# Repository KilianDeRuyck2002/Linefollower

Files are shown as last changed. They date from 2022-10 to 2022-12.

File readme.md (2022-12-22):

# LineFollower

<br />

## specifications
microcontroller: ATmega328 (Arduino Nano)
<br />
motors: Gear motor 9V - 10:1
<br />
h-bridge: Adafruit TB6612
<br />
sensors: QTR-8A
<br />
batteries: Lipo 3S 11,1V
<br />
wireless communication: HC-05
<br />
distance sensor - motors: 110mm
<br />
weight: 220g
<br />
speed: 0,906 m/s
<br />

## tips
<br />
1) Zorg dat de batterij zo dicht mogelijk bij de motoren staan. Zorg dat deze een beetje voor de hartlijn van de motoren ligt zodat de line follower geen wheelie maakt maar toch het grootste gewicht ligt bij de aandrijving.
<br />
<br />
2) Door de motoren breder uit elkaar te plaatsen kan hij de bochten makkelijker nemen.
<br />
<br />
3) Zorg dat de sensoren niet te ver en niet te dicht t.o.v. de motoren liggen. Als dit zich bevindt verder van de motoren zal je makkelijker aan een grotere snelheid komen maar kan je wel in de problemen geraken in scherpe bochten.
<br />
<br />
4) Hoe kleiner de diameter van de wielen hoe sneller de line follower zal gaan.
<br />
<br />
5) In het begin is er gebruik gemaakt van een bout maar deze bracht veel weerstand met zich mee, daarom is er overgeschakeld naar een bol (deze heeft maar 1 contactpunt met het papier, dus de weerstand is hier minimaal).
<br />
<br />
6) Bij de finaal code zal er een code te vinden zijn met library en zonder. De line follower is even snel met beide codes, alleen voor het programma kleiner te maken is het handig om met de library te werken.
<br />
<br />
7) Ook is er een finaal code geupload met een boost en brake principe, deze zal steeds voor de lange rechte stukken versnellen en dan bij de eerst volgende bocht kort remmen.
<br />
<br />
8) Tip voor de motoren, kies voor de gearmotoren 1000rpm / 30:1.
<br />
<br />

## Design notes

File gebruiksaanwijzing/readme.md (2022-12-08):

# Gebruiksaanwijzing

Zie document 

### opladen / vervangen batterijen
Deze line follower werkt met Lipo batterijen.

### draadloze communicatie
#### verbinding maken
uitleg over het verbinden van de robot met laptop / smartphone

#### commando's
debug [on/off]  
start  
stop  
set cycle [µs]  
set power [0..255]  
set diff [0..1]  
set kp [0..]  
set ki [0..]  
set kd [0..]  
calibrate black  
calibrate white  

### kalibratie
uitleg kalibratie  

### settings
De robot rijdt stabiel met volgende parameters:  

### start/stop button
uitleg locatie + werking start/stop button

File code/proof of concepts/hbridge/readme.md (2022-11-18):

# H-Bridge proof of concept

Minimale hard- & software die aantoont dat 2 motoren onafhankelijk van elkaar kunnen draaien, en (traploos) regelbaar zijn in snelheid en draairichting.

Programma:
- Voorwaarts van 0 -> 255 -> 0
- Achterwaarts van 0 -> 255 -> 0
- Links van 0 -> 255 -> 0
- Rechts van 0 -> 255 -> 0

Sidenote: DRV8833 mag een maximale spanning van 10,8V bedragen.
- Indien dit hoger is, dan zal de bluetooth module maar 3 weken meegaan zoals in mijn geval geweest.

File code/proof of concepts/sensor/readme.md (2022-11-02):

# Sensoren proof of concept

minimale hard- en software die aantoont dat minimaal 6 sensoren onafhankelijk van elkaar kunnen uitgelezen worden en dat daarbij een zo groot mogelijk bereik van de AD converter benut wordt (indien van toepassing)

Programma:
- Uitlezing van (8) sensoren => (QTR-8A)

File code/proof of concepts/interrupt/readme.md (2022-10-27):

# start/stop interrupt proof of concept
Minimale hard- en software die de correcte werking van een start/stop drukknop aantoont, gebruik makend van een hardware interrupt

Programma:
- Led in het begin uit
- Indien er op de interrupt knop wordt geklikt zal de status van de led veranderen
  - Van low naar high (led gaat aan)
  - Van high naar low (led gaat uit)

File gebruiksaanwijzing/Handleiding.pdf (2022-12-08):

# Handleiding Line follower

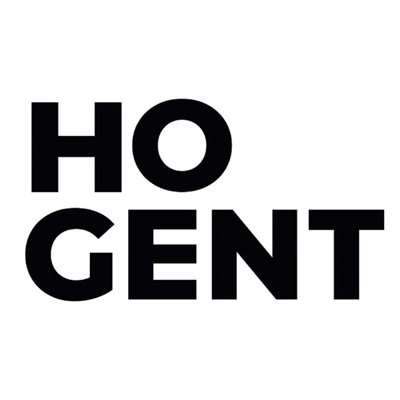
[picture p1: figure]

Naam: De Ruyck
Voornaam: Kilian
Klasgroep: 3AMB

## Gebruik van de line follower

Voor de line follower te laten rijden moeten eerst alle parameters worden ingesteld en moeten de sensoren worden gekalibreerd.

Kalibreren
Voor de sensoren te kalibreren moet er in de seriële monitor via de computer of bluetooth module het commando “calibrate white” of “calibrate black” worden getypt. Indien het commando is doorgestuurd zal deze de waarden opslaan. Zorg er wel voor dat de line follower op een volledige witte ondergrond staat om de witte waarden op te slaan en bij de zwarte waarden op een volledige zwarte ondergrond.

Rijden
Nu kunnen de parameters worden doorgestuurd aan de hand van de commando’s. Met het commando “run” zal de line follower starten met rijden. Bij het commando “stop” zal deze stoppen met rijden. Indien een commando wordt doorgestuurd die fout geschreven is of onjuist is zal er een message verschijnen dat deze niet gevonden is, dus er kan niets kapot gaan door een fout commando door te sturen.

De commando’s
- “run” => Starten met rijden (dit kan ook met de knop gedaan worden)
- “stop” => Stoppen met rijden
- “debug” => Tonen van de ingestelde parameters met de waarden
- “calibrate” => Calibreren van de sensoren
- “set cycle ‘waarde’ ” => Set cycle naar ‘waarde’ (waarde moet cijfer zijn)
- “set power ‘waarde’ ” => Set power naar ‘waarde’ (waarde moet cijfer zijn)
- “set diff ‘waarde’ ” => Set diff naar ‘waarde’ (waarde moet cijfer zijn)
- “set kp ‘waarde’ ” => Set kp naar ‘waarde’ (waarde moet cijfer zijn)
- “set ki ‘waarde’ ” => Set ki naar ‘waarde’ (waarde moet cijfer zijn)
- “set kd ‘waarde’ ” => Set kd naar ‘waarde’ (waarde moet cijfer zijn)

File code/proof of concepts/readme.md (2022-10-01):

# Proof of Concepts

Een proof of concept is een combinatie van minimale hard- en software om eenvoudig aan te tonen dat iets werkt.  
Proof of concepts kunnen enerzijds als eerste poging dienen om een bepaald onderdeel van het project werkend te krijgen. Anderzijds kunnen ze tijdens het debuggen van het finale project dienen als test om eventuele hardware problemen te elimineren bij onduidelijke problemen.
<br />  
<br />
Een proof of concept bestaat uit
* een elektronisch schema (indien van toepassing)
* minimale code om de voorop gestelde zaken te demonstreren
* minimale uitleg / aandachtspunten
<br />
De elektronische schakelingen van de proof of concepts komen bij voorkeur overeen met deze van de uiteindelijke linefollower, zodat de code zonder aanpassingen op het finale project kan draaien.

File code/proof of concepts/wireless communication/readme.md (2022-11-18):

# draadloze communicatie proof of concept
minimale hard- en software waarmee aangetoond wordt dat duplex kan gecommuniceerd worden tussen de microcontroller en een [laptop|smartphone] (schappen wat niet past), gebruik makend van [programma] (in te vullen)
<br />
### configuratie
Code HC-05: 0000 of 1234

### opmerkingen
Gebruik gemaakt van de "Serial Bluetooth Terminal" app

### gebruiksaanwijzing
/

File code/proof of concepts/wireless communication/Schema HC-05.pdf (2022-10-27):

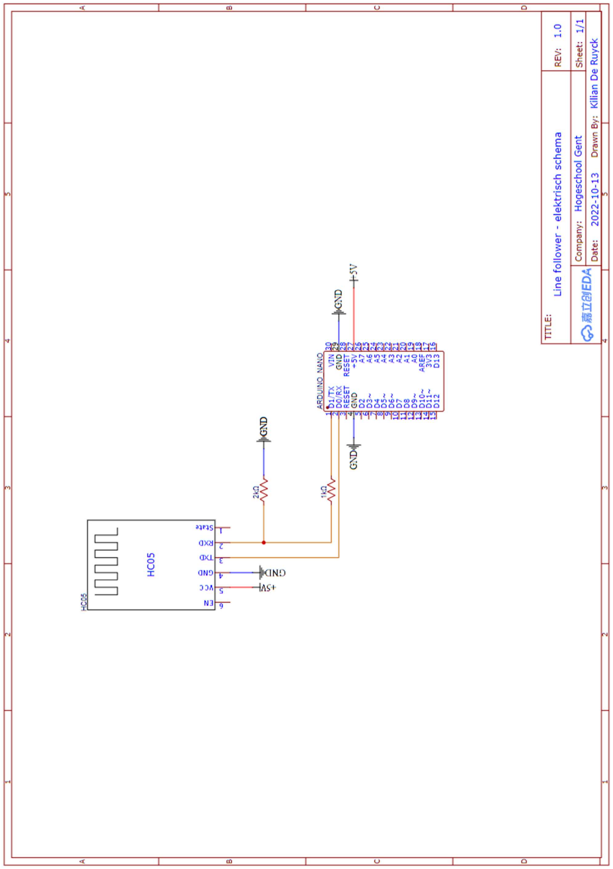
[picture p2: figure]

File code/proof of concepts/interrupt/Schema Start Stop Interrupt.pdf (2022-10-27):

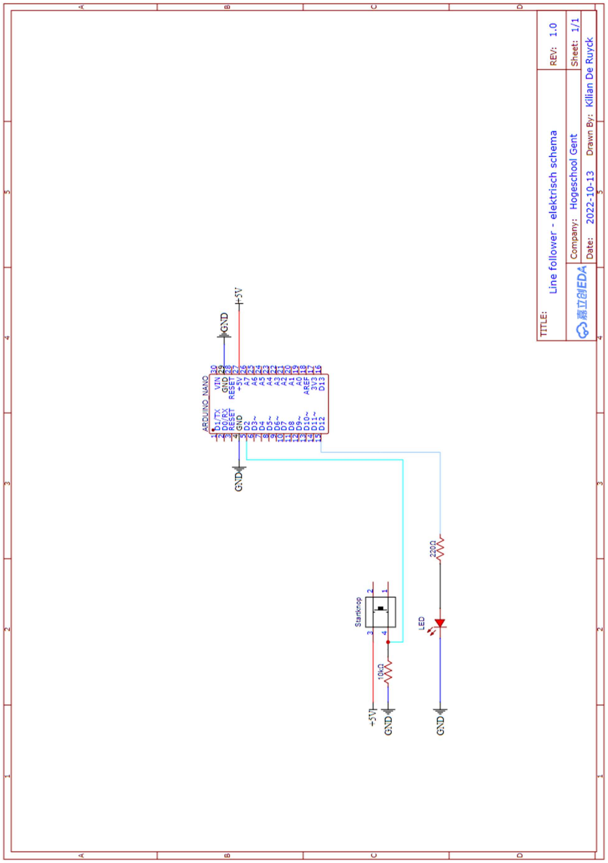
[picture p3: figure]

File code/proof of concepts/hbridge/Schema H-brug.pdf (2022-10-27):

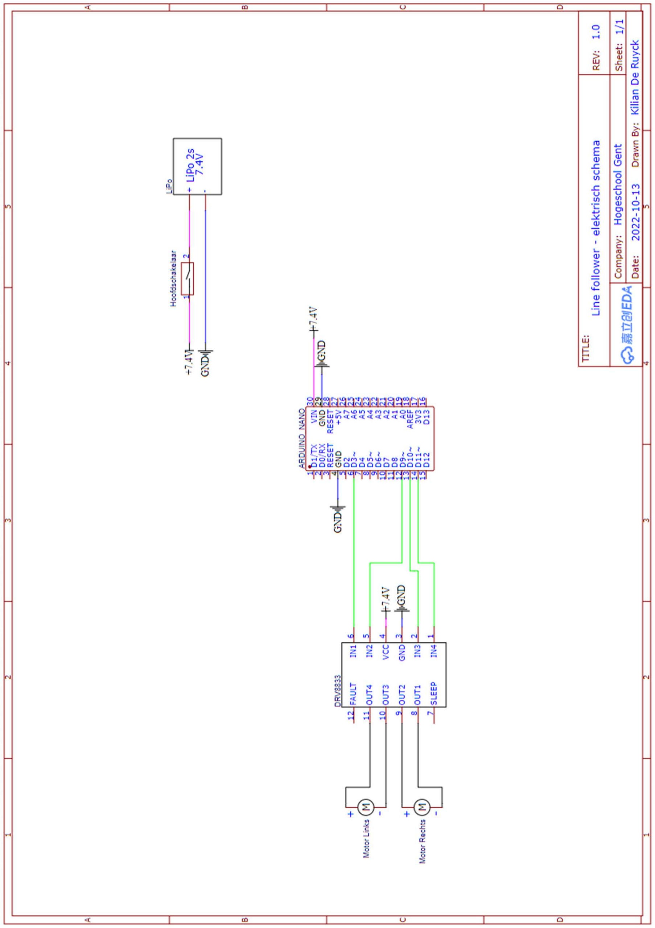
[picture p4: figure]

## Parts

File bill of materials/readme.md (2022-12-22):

## bill of materials
<br />

|Nr.  |Naam |Omschrijving |Nieuw/recup|Prijs/Stuk|Aantal|Subtotaal|
|-----|---|---|---|---|---|---|
|1 |Microcontroller	 |ATmega328 (Arduino Nano)	 |Nieuw |€ 5,4	 |1	 |€ 5,4 |
|2	  |Sensoren	 |QTR-8A	 |Nieuw |€ 11,91 |1	 |€ 11,91  |
|3	  |H-brug	 |TB6612	 |Nieuw |€ 6,5	 |1	 |€ 6,5 |
|4	  |Bluetooth module	 |HC-05	 |Nieuw |€ 4	 |1	 |€ 4 |
|5	  |Motoren	 |Gear motor 9V - 10:1	 |Nieuw |€ 5,4 |2	 |€ 10,8 |
|6	  |Wielen	 |Wielen pair 32x7mm	 |Nieuw |€ 4,32	  |1	 |€ 4,32 |
|7	  |Batterij	 |Sunpadow 3S 11,1V	 |Nieuw |€ 14,5 |1	 |€ 14,5 |
|8	  |Led	 |Led blauw 5V	 |Recup |€ 0	 |1	 |€ 0 |
|9	  |Drukknop	 |Drukknop 	 |Recup |€ 0	 |1	 |€ 0 |
|10	  |Schakelaar	 |Mini wipschakelaar AAN/UIT	 |Recup |€ 0	 |1	 |€ 0 |
|11	  |Weerstand	 |Weerstand 220Ω	 |Recup |€ 0	 |1	 |€ 0 | 
|12	  |Weerstand	 |Weerstand 1kΩ	 |Recup |€ 0	 |3	 |€ 0 |
|13	  |Weerstand	 |Weerstand 10kΩ	 |Recup |€ 0	 |1	 |€ 0 |
|14	  |Prototype Board |Double shielded board 50x70mm	 |Nieuw |€ 0,98	  |1	 |€ 0,98 |
|15	  |Frame	 |PLA	 |Nieuw |€ 0,34	  |1	 |€ 0,34 |
|16	  |Klemmenstrook	 |4 aansluitingen |Recup |€ 0 	  |1	 |€ 0 |
| | | | | |Totaal prijs:|€ 58,75  |

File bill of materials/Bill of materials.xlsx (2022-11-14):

Nr. | Naam | Omschrijving | Nieuw/Recup | Prijs/stuk | Aantal | Subtotaal | Link
1 | Microcontroller | Arduino Nano | Nieuw | 5.4 | 1 | 5.4 | https://www.amazon.nl/gp/product/B078S8BJ8T/ref=ppx_yo_dt_b_asin_title_o03_s00?ie=UTF8&psc=1
2 | Sensoren | QTR-8A | Nieuw | 11.91 | 1 | 11.91 | https://botland.store/sensors-odbiciowe/152-qtr-8a-reflectance-sensor-array-analog-pololu-960-5903351249300.html
3 | H-brug | TB6612 | Nieuw | 6.5 | 1 | 6.5 | https://www.kiwi-electronics.com/nl/adafruit-tb6612-1-2a-dc-stepper-motor-driver-breakout-board-2188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
4 | Bluetooth module | HC-05 | Nieuw | 4 | 1 | 4 | https://www.amazon.nl/gp/product/B07BHRG9KB/ref=ppx_yo_dt_b_asin_title_o03_s00?ie=UTF8&psc=1
5 | Motoren | Gear motor 9V -10:1 | Nieuw | 5.4 | 2 | 5.4 | https://botland.store/n20-micro-motors-mp-series-medium-power/12551-micro-motor-n20-bt12-10-1-1300rpm-9v-5904422306526.html
6 | Wielen | Wielen pair 32x7mm | Nieuw | 4.32 | 1 | 4.32 | https://botland.store/wheels-with-tires/12-wheels-32x7mm-black-2pcs-pololu-1087-5903351247924.html
7 | Batterij | Sunpadow 3S 11,1V | Nieuw | 14.5 | 1 | 14.5 | https://www.amazon.nl/gp/product/B08S37P8Z5/ref=ppx_yo_dt_b_asin_image_o00_s02?ie=UTF8&psc=1
8 | Led | Led blauw 5V | Recup | 0 | 1 | 0 | https://www.allekabels.be/led-diode/7369/1086017/blauwe-led-3mm-transparant-2200mcd-20ma.html
9 | Drukknop | Drukknop | Recup | 0 | 1 | 0 | https://www.otronic.nl/a-60343296/schakelaars/drukknopje-moment-6x6x4/
10 | Schakelaar | Mini wipschakelaar AAN/UIT | Recup | 0 | 1 | 0 | https://www.otronic.nl/a-62577459/schakelaars/mini-wipschakelaar-aan-uit-kcd11-250v-3a/
11 | Weerstand | Weerstand 220Ω | Recup | 0 | 1 | 0 | https://www.otronic.nl/a-59685595/weerstanden/10x-weerstand-220-ohm-1-4-watt-5-led-voorschakelweerstand/
12 | Weerstand | Weerstand 1kΩ | Recup | 0 | 3 | 0 | https://www.otronic.nl/a-59867443/weerstanden/10x-weerstand-1k-ohm-1-4-watt-5/
13 | Weerstand | Weerstand 10kΩ | Recup | 0 | 1 | 0 | https://www.otronic.nl/a-59867467/weerstanden/10x-weerstand-10k-ohm-1-4-watt-5-pull-up-pull-down/
14 | Prototype board | Double shielded board 50x70mm | Nieuw | 0.98 | 1 | 0.98 | https://botland.store/circuit-boards/2745-universal-double-sided-board-50x70mm-5904422303303.html
15 | Frame | PLA | Nieuw | 0.34 | 1 | 0.34 | /
Totaal prijs: |  |  |  |  |  | 53.35

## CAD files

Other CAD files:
technische tekeningen/mechanisch/Assembly Line follower.iam
technische tekeningen/mechanisch/Ball houder plaat.ipt
technische tekeningen/mechanisch/Bracket motoren.ipt
technische tekeningen/mechanisch/Dubbele wiel.ipt
technische tekeningen/mechanisch/Frame.ipt
technische tekeningen/mechanisch/Sensoren plaat.ipt

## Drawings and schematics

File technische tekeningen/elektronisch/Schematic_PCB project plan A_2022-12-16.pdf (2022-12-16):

# HC-05 HC⁻05 VCC

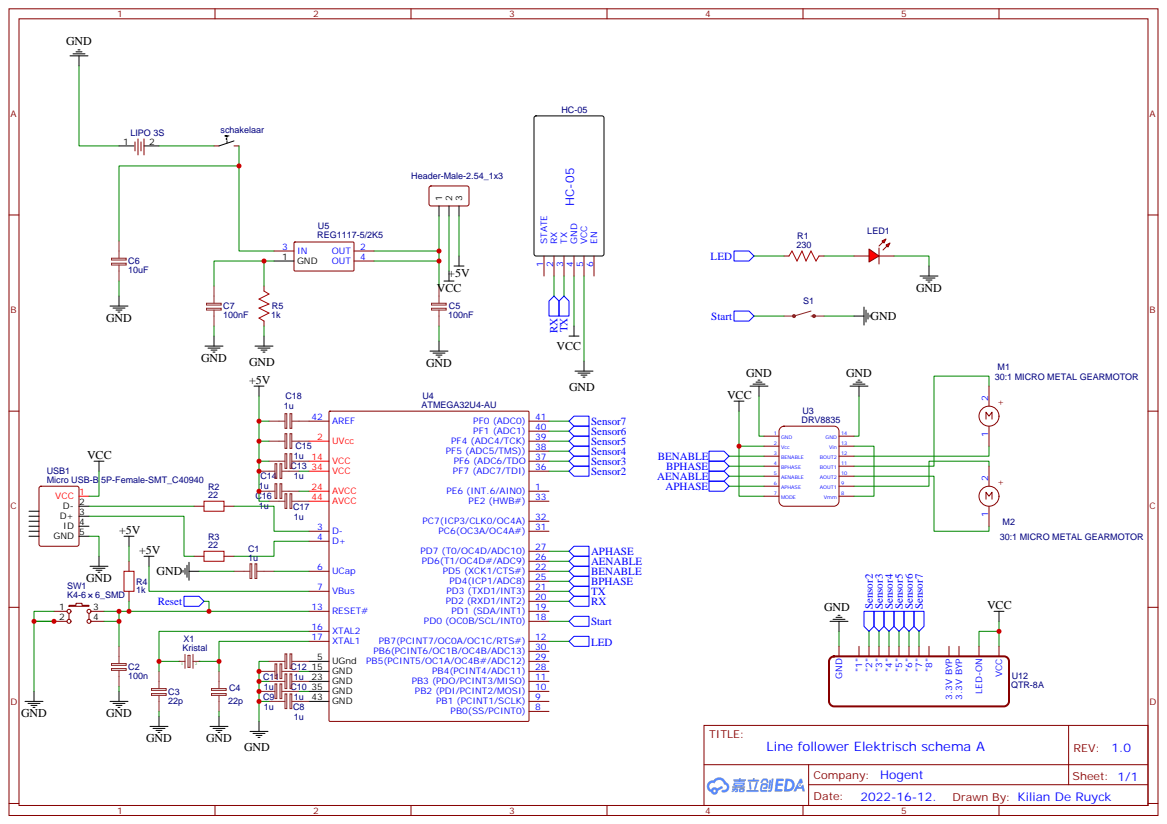
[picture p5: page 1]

PB7(PCINT7/OC0A/OC1C/RTS#) 12
PB2 (PDI/PCINT2/MOSI) 10 PB3 (PDO/PCINT3/MISO) 11 PB4(PCINT4/ADC11) 28 PB5(PCINT5/OC1A/OC4B#/ADC12) 29 PB6(PCINT6/OC1B/OC4B/ADC13) 30

Drawn By: Kilian De Ruyck

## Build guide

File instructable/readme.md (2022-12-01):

# Instructable

Een instructable is een stappenplan - zonder verdere uitleg - hoe je vertrekkend van de bill of materials en gebruik makend van de technische tekeningen de robot kan nabouwen. Ook de nodige stappen om de microcontroller te compileren en te uploaden staan beschreven.  

### stap 1
Zie document

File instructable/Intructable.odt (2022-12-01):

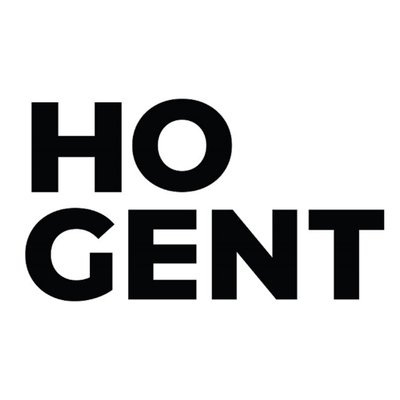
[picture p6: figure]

Intructable

Line follower

Naam: De Ruyck
Voornaam: Kilian
Klasgroep: 3AMB

Inhoudsopgave

1. Inleiding

In deze instructable wordt stap voor stap uitgelegd hoe de line follower gemaakt wordt. Hierbij zal er aan de hand van een schema uitgelegd worden hoe de verbindingen gemaakt moeten worden. Wel wordt er verwacht dat er een basiskennis is over solderen en elektriciteit.

2. Benodigdheden
- 3D-printer
- Soldeerbout
- Soldeertin
- Pinheaders male en female
- Bevestigingen (moeren, bouten en klitteband)
- USB mini kabel
- Componenten (terug te vinden in de BOM)
3. Elektrische schema

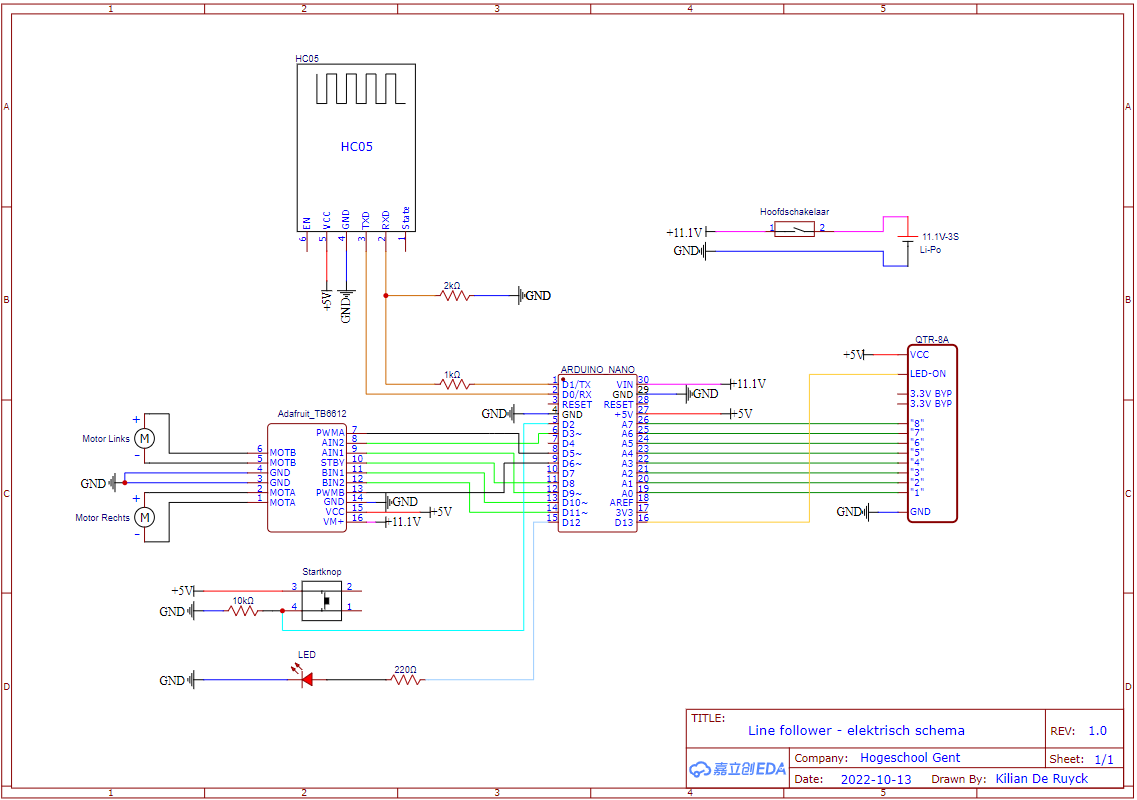
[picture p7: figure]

4. Stappenplan

Stap 1

Eerst moeten de brackets voor de motoren, het frame, de dubbele wielen (indien gewenst), de plaat van de sensoren en van de ball mounting ge-3D-print worden. De print files kunnen gevonden worden in de github.

Frame Sensor plaat

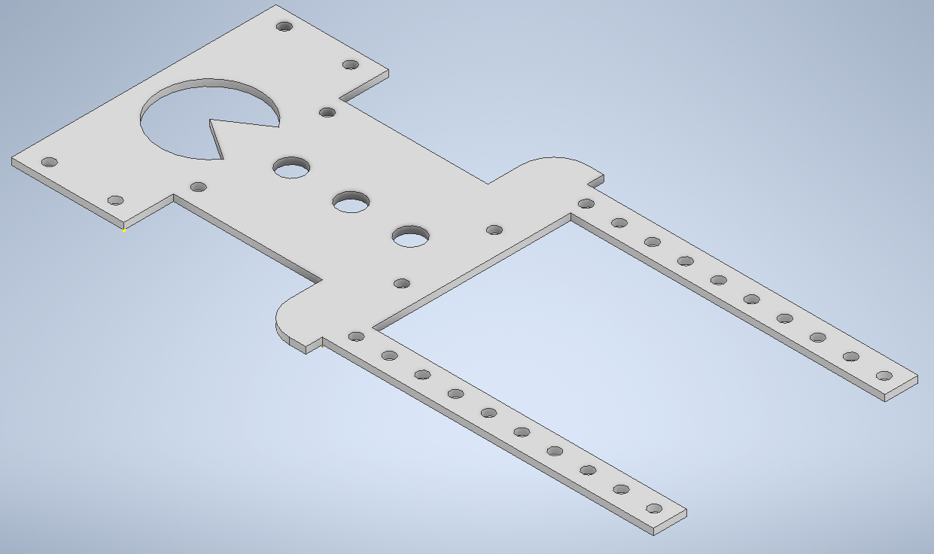
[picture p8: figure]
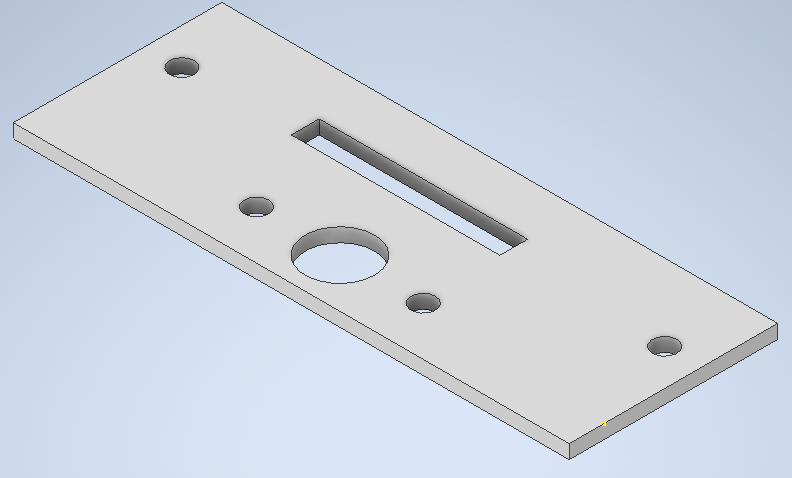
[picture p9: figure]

Bracket motoren Ball mounting plaat Dubbele wiel

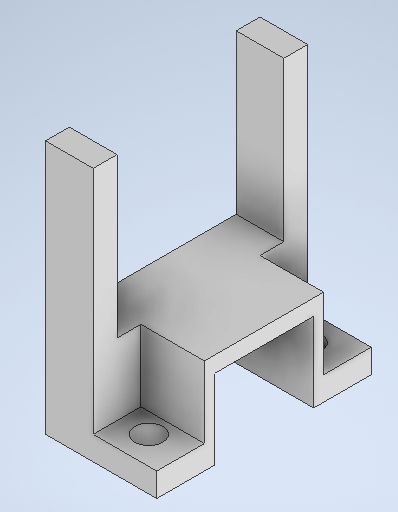
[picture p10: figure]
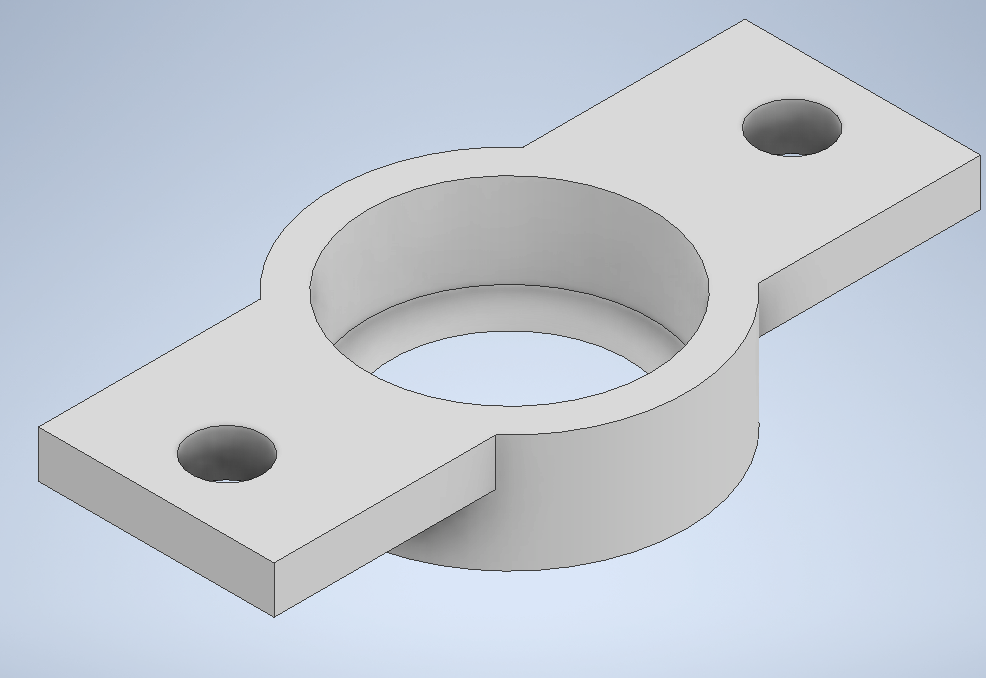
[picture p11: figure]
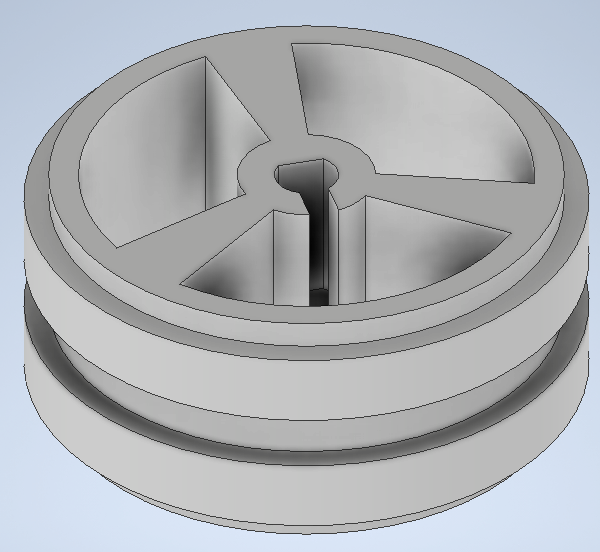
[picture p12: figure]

Stap 2

In deze stap zal de printplaat worden gesoldeerd. Hierbij kan er aan de hand van onderstaande foto’s en het elektrische schema een werkend printplaat worden verkregen.

Pinout:

- D0 = TX HC-05 - D1 = RX HC-05
- D2 = Startknop - D3 = Ain2
- D5 = PWMA - D6 = PWMB
- D8 = Standby - D9 = Ain1
- D10 = Bin1 - D11 = Bin2
- D13 = LedOn - A0 t.e.m. A7 = Sensoren

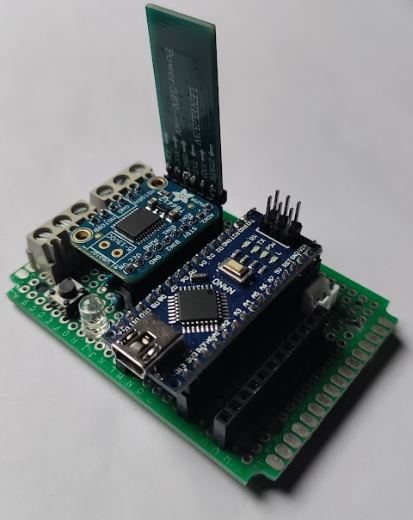
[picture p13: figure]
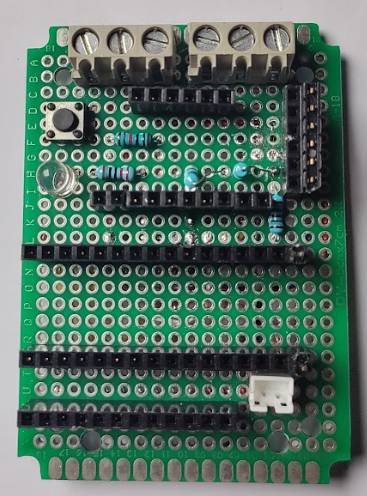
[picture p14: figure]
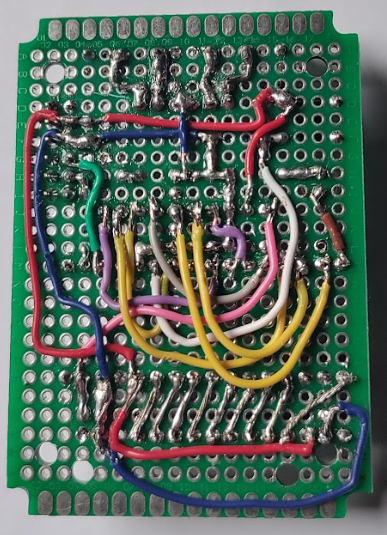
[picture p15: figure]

Stap 3

Nu moeten er aan de hand van de moeren en bouten de motoren met brackets, sensoren en printplaat worden bevestigd aan het frame. De sensoren kunnen aangesloten worden met Dupont draden.

De wielen kunnen gewoon over de motoren geschoven worden. Net zoals bij de batterij tussen de brackets.

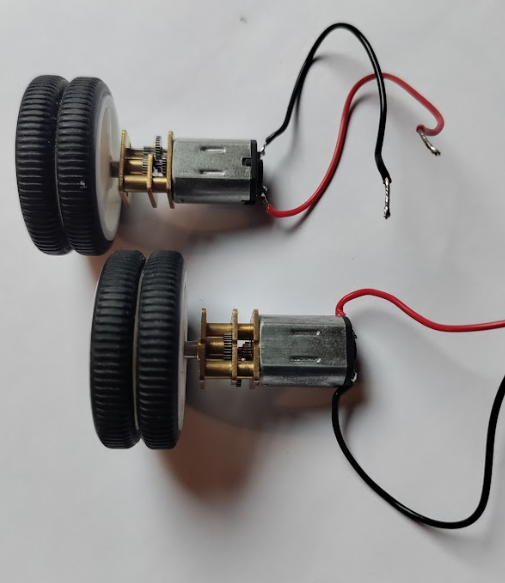
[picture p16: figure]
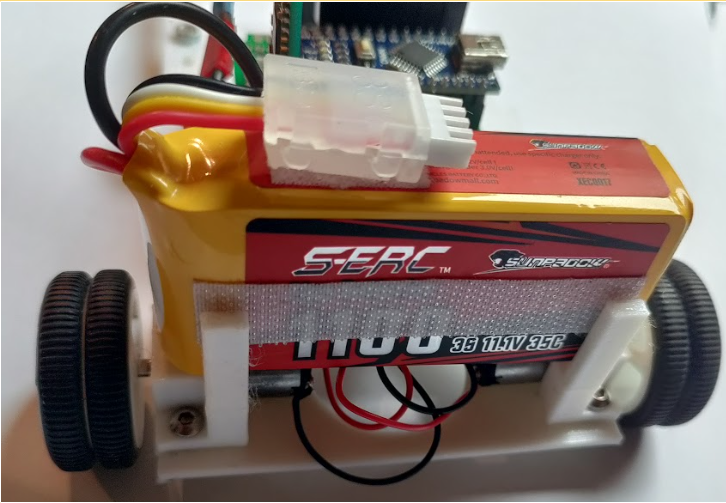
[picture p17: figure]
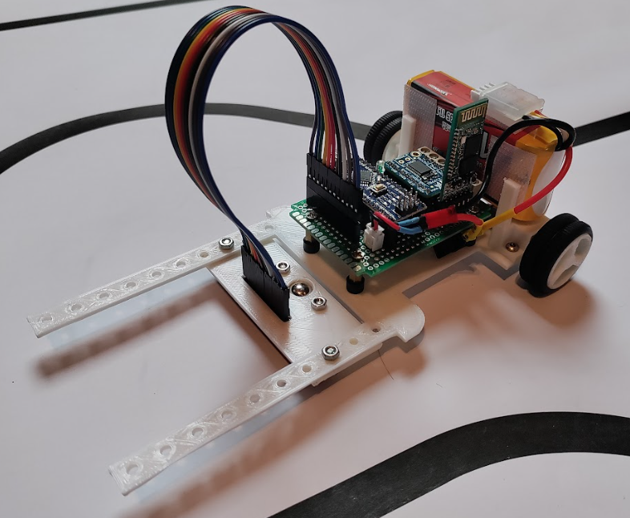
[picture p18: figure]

5. Installeren van de software

Nu de line follower fysiek in elkaar zit en geen fouten gemaakt zijn tijdens de stappen kan er nu over gegaan worden naar het programmeren.

Eerst en vooral zal de Arduino IDE software moeten gedownload worden. Deze kan terug gevonden worden op de Arduino site (https://www.arduino.cc/en/software). In mijn geval heb ik versie 1.8.16. Er kunnen oudere en nieuwere versies gedownload worden, maar weet dat dit soms errors met zich kan meebrengen.

Nu de software aanwezig is kan het programma gedownload worden. Hierbij zal er connectie moeten gemaakt worden tussen de Arduino Nano en de computer via de micro USB kabel. Weet wel dat wanneer er connectie gemaakt wordt dat er een spanning aanwezig zal zijn op het prototype bord, dus controleer eerst zeker dat er nergens een kortsluiting kan gemaakt worden. Anders zullen er componenten beschadigd kunnen worden.

Bij het downloaden van het bestand moet er wel nog bekeken worden dat de libraries mee gedownload worden. Het beste dat er kan gedaan worden is om de zip map te downloaden en deze uit te pakken, normaal zouden alle libraries dan al goed moeten staan.

- Seriële communicatie

Om met de Arduino te communiceren kun we dit doen aan de hand van de Usb kabel tussen de Arduino en de computer. Hierbij zal er gewerkt worden met de seriële monitor en/of seriële plotter. Er kan ook communicatie gemaakt worden aan de hand van de HC-05, die hetzelfde gedrag zal vertonen als er wordt gewerkt via de computer.

- De parameters

Om de line follower optimaal te laten werken zijn de parameters een van de belangrijkste zaken in deze code. Hierbij kunnen we de parameters Cycle, Power, Diff, Kp, Ki en Kd instellen.

Cycle: De cycle is de tijd die de Arduino gebruikt om het programma op een vast interval uit te voeren. De cycle tijd zal afhangen van de calculation tijd (tijd die de Arduino nodig heeft om het programma uit te rekenen), de cycle tijd moet altijd boven de calculation tijd liggen.

Power: Deze zal rechtsreeks de snelheid van de motor gaan veranderen, hoe hoger/kleiner de power hoe hoger/kleiner het toerental van de motoren. Deze kan liggen tussen de 0 en 255. Om te starten is het gewenst om dit op 40 à 50 te zetten.

Diff: Deze parameter zal helpen bij het vermogen van de motor in verband met de snelheid. De snelheid van de motor is namelijk niet evenredig met het vermogen. Deze parameter moet liggen tussen de 0 en de 1. Indien de line follower stil valt zal je deze parameter moeten vergroten, indien deze uit de bocht vliegt zal de parameter moeten verkleind worden.

Kp: Bij een grote fout gaat er sterk worden bijgestuurd en bij een kleine fout zal er maar een klein beetje worden bijgestuurd.

Ki: Hier zal er worden gekeken hoe lang de fout zich voordoet, hoe langer de fout hoe groter de som zal worden waardoor de fout sterker wordt bij geregeld.

Kd: Hier wordt er gekeken hoe snel de fout veranderd, als het verschil uit de vorige cyclus groot is dan gaat er sterk bijgestuurd worden. Als het verschil klein is dan zal er minder sterk worden bijgestuurd.

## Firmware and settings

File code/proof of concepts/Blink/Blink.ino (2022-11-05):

const int LedBlauw = 12;

void setup() {
  Serial.begin(9600);
  pinMode(LED_BUILTIN, OUTPUT);
  pinMode(LedBlauw, OUTPUT);
}

void loop() {
  digitalWrite(LED_BUILTIN, HIGH);   // turn the LED on (HIGH is the voltage level)
  digitalWrite(LedBlauw, HIGH);
  delay(1000);                       // wait for a second
  digitalWrite(LED_BUILTIN, LOW);    // turn the LED off by making the voltage LOW
  digitalWrite(LedBlauw, LOW);
  delay(1000);                       // wait for a second
}
